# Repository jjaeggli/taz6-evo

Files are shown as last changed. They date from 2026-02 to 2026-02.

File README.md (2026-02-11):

# TAZ6-Evolution

- [Purpose](#purpose)
- [Summary](#summary)
- [Caution!](#caution)
- [Design Philosophy](#design-philosophy)
- [Current Progress](#current-progress)
- [BOM](#bom)
- [Printed Parts](#printed-parts)
- [Assembly Instructions](#assembly-instructions)
  - [Required Tools](#required-tools)
  - [Disassembly](#disassembly)
  - [Heat Set Inserts](#heat-set-inserts)
    - [Z1 Axis](#z1-axis)
    - [Bearing Block](#bearing-block)
    - [Mounting Plate](#mounting-plate)
  - [Assembly](#assembly)
    - [X-Axis Carriage](#x-axis-carriage)
    - [Z1-Axis Traveler](#z1-axis-traveler)
    - [X-Z Axis Tuning](#x-z-axis-tuning)
    - [Belt Binder](#belt-binder)
    - [Accessories](#accessories)

## Purpose

Allow the Lulzbot TAZ6 to experimentally support other tool options, and to improve the rigidity and performance of the toolhead.

## Summary

A series of evolutionary modifications for the Lulzbot TAZ6 and possibly other TAZ series 3D printers. The goal of the modifications are to allow adapting the printer to different toolhead designs by introducing modifications to the X-axis carriage, and to improve the rigidity of the toolhead by creating additional mount points. As a prerequisite, modifications must be made to the Z-axis to adjust the angle and position of the X-axis belt. The result is a series of evolutionary steps necessary to redesign the Taz while maintaining existing functionality at each step.

## Caution!

These designs have not yet been tested beyond one TAZ6 printer, and required troubleshooting and problem solving at each step. Individualized tweaks to the design may be required for your printer which were not required for mine. If you disassemble parts such as the original X-axis carriage to use the existing Igus bearings, this may destroy the part. These designs come without warranty, and any loss or damage is your responsibility.

* This design does not take into account the X or Z-max endstops, which are not used by Klipper
* Work on the left hand (motor side) Z-traveler is incomplete and untested

## Design Philosophy

* Move forward in reversable steps
* Reuse hardware from the original printer where possible
* Predict future use cases without setting specific untested requirements
* Design iteratively and start from scratch often
* (1) Make it work, (2) make it correct, (3) make it perform (pretty, optimal, light weight, etc...)

## Current Progress

- [x] Modification of the right Z-gantry traveler
  * reposition the idler pulley at the midpoint between the X rails.
  * convert the composite Igus bearing to LM10LUU (55mm) linear bearings to simplify design and assembly.
  * add affordances for future modifications (motor mount, dual X axis pulleys).
- [x] Modification of the X-carriage
  * reduce the overall width of the X carriage to 60 mm.
  * improve vertical and horizontal symetry of the carriage.
  * align the belt with the midpoint of the X-axis rails
  * improve the belt binder to reduce flexibility
  * add mount points for hard mounting components
- [x] Modification of the tool mount plate
  * add mount points to the plate to allow tools to be directly mounted to the plate.
  * add mount points for TAZ quick tool change mounts.
- [ ] Modify motor mount for right side (Z0)
  * adjustable belt tension on motor mount
  * support mulitple motor / belt positions
- [ ] Modify motor mount for left side (Z1)
  * support dual stepper motors
  * adjustable belt tension on motor mount

## BOM

* An assortment of M3 hex socket screws sizes 4mm - 25mm including nuts
* A handful of M3 poly washers
* A bunch of M3 5.5mm x 4mm heat set inserts
* (4) M5 heat set inserts (mine are M5 x 9.5) 
* (2) M5 x 25mm hex socket screw
* (2) M5 nylon lock nuts 
* (1) 20T GT2 idler pulley with 5mm bore
* (2) LM10LUU linear bearings
* (4) LM12UU IGUS solid polymer bearings RJ4JP
* (1) Lulzbot TAZ6 printer
* This list could be incomplete

## Printed Parts

| Qty | Material | Name | Desc |
|---|---|---|---|
| 2 | PETG | TAZ6-x-carriage-v0.5-BearingUniversal | Igus bearing block |
| 1 | PLA / ABS | TAZ6-x-carriage-v0.5-BeltTensioner | Belt tensioner / retainer |
| 1 | PLA / ABS | TAZ6-x-carriage-v0.5-EndStopClicker | Only necssary when not using the TazMount toolhead adapter |
| 1 | PLA / ABS | TAZ6-x-carriage-v0.5-MountingPlate | X-axis carriage mounting plate |
| 1 | PLA / ABS | TAZ6-x-carriage-v0.5-TazMount | Lower mounting bracket for TAZ quick mout toolheads |
| 1 | PLA / ABS | TAZ6-x-carriage-v0.5-TazMountTop | Upper mount point for TAZ quick mount toolheads |
| 1 | PETG | TAZ6-z-axis-v0.3-Z1-Axis | Right (Z1) axis |
| 0 | PETG | TAZ6-z-axis-v0.4-Z0-Axis | Left (Z0) axis - *unused* |

## Assembly Instructions

*These aren't really instructions per se, more like guidelines.*

### Required Tools

* 2.5 mm hex key
* 3 mm hex key
* 4 mm hex key
* Adjustable wrench or metric socket set
* Low temp soldering iron for insets
* Cubes of equal height (at least 40mm) that you can use as standoffs (such as stacked calibration cubes)

### Disassembly

Adjust the gantry height so that the standoff cubes are just barely held in place between the lower X-axis rod and the green lower Z-axis assembly on the right hand side. This will be used later in the process to ensure that the rods are attached squarely.

Disassemble and remove the X-axis belt, the X-axis rods, the X-axis carriage (removed from the rods), and the right top plate.

Unscrew the two M5 screws from the right lead screw nut (threaded flange). Reserve these screws. Remove the right Z-axis traveler. Reserve the green lead screw spacer.

Unplug the right stepper motor connector.

### Heat Set Inserts

Note: There are many available positions for heat set inserts - more than you will actually need. Install only the ones necessary for your specific use case at this point.

#### Z1 Axis

* (2) M3 inserts for securing the rods. (top and bottom)
* (2) M5 insers for attaching the lead screw nut. (12:00 and 6:00 position when facing the printer)

#### Bearing Block

* (2) M3 inserts on the top of one universal bearing block (this block will now be the top block)

#### Mounting Plate

All inserts on the mounting plate are optional. Hex nuts are used for all pull-through hardware and for convenience during prototyping. Mounting the *TAZ-EVO* toolhead components requires use of insets. 

### Assembly

#### X-Axis Carriage

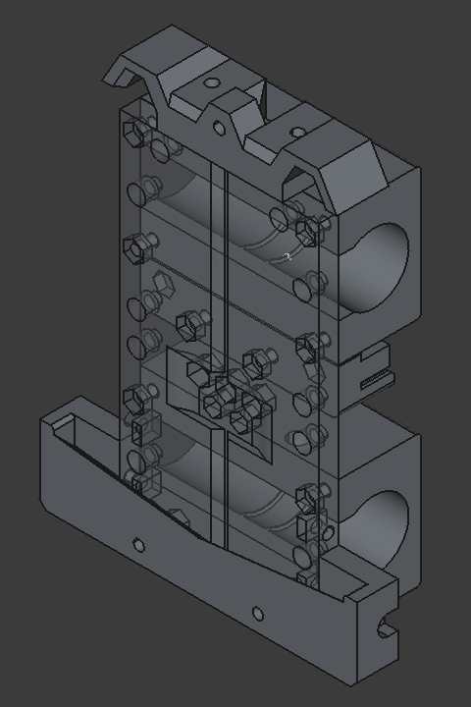
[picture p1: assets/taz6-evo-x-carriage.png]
X-carriage


* Sand and trim the inside of both `BearingUniversal` blocks.
* Snap Igus bearings in place. (Be careful as they do easily pinch skin)
* Test the blocks on one loose end of a rod. If the block is too tight / does not travel easily, remove the bearings and perform some additional sanding and trimming on the retaining rings inside the block.
* Fit (2) M3 nuts for the TAZ mount into the *back* of `MountingPlate` (the back is the side without the groove).
* Attach the bearing blocks with (4) M3 x 25mm screws and (4) M3 nuts for each block. The screws should be somewhat loose but still engaged in the nuts.

#### Z1-Axis Traveler

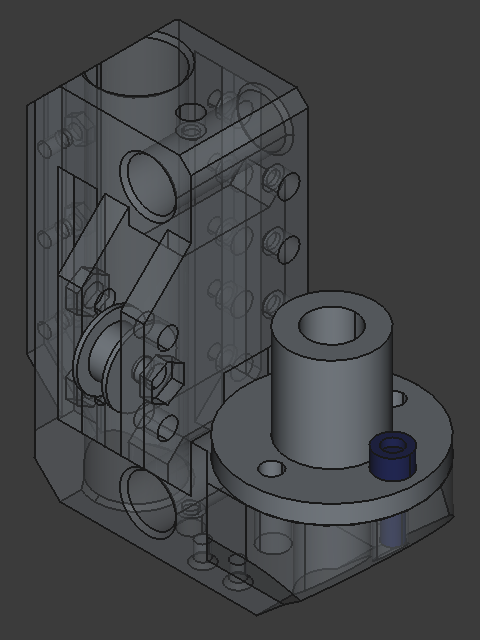
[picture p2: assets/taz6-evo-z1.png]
Z1-Axis


* Fit (1) LM10LUU bearing into position and secure with (3) M3 x 10mm screws and (3) M3 x 10mm nuts
* Fit (1) M5 x 25mm screw in place with the idler pulley in the center position and secure with the lock nut.
* Screw (2) M3 x (smallest that works) screw in each heat set insert. Test that when tightened the screw engages the rod and prevents movement. Leave loose.
* Slide the Z-axis traveler over the two rods, and slide it down to the bottom.
* Insert the X-axis rods through the traveler from the right hand side, so that they extend on each side.
* Slide the X-carriage over the the X-axis rods.
* Slide the X-axis rods throug the right Z-traveler until they reach the left Z-traveler, and use the standoff blocks to ensure that the rods are at the correct height.
* Add the green lead screw spacer, and then thread the lead screw nut until it is approximately in position. Thread the reserved M5 screws into the nut and adjust them until they are just loose.
* Using the spacer between the X-axis rods, and any other measurement tools at your disposal, ensure that the X-axis is square and level. Tighten grub screws on the left side and the M3 screws on the right side to secure the rods in place. 
* Ensure that the X-carriage still travels freely, and the lead screw turns easily.
* Reinstall the top plate on the Z-axis, ensuring that the extrusions are square when tightening.
* Follow the instructions below for tuning the X-Z axis

#### X-Z Axis Tuning

The X and Z axes intersect at the junction of the X-axis rails, and the Z-axis rail and lead screw. The Z-traveler holds the Z-axis linear bearing, the lead screw nut, the X-axis linear rails, and secures the belt. All of these parts must be properly aligned for the Z-traveler to move freely in the Z direction.

* At each step durring the assembly, the lead screw should be checked to ensure it rotates freely by turning it back and forth slightly. It should turn easily. If it is difficult to turn, the previous step introduced binding.
* Disconnnecting the power connector from the motor will ensure that there is not additional electromagnetic load on the motor (even when the printer is off)
* The X-axis rails oppose the force applied by the belt. If there is tension on the belt when the rails are loose, this can cause leadscrew binding. *You must loosen the belt before loosening the X-axis rails.*
* The X-axis belt must be loose when tuning the X-Z Axis.
* The squishy yellow-green spacer allows the leadscrew nut *tilt* to be properly aligned.
* When tightening the M4 screws on the lead screw nut, tighten them a quarter turn at a time, alternating between each, and checking the lead screw binding at each step. If the lead screw binds, loosen the screw and tighten the *opposite* screw.

#### Belt Binder

* The binding block holds the belt securely in place, and provides coarse tuning for belt tension.
* The stepper motor mount provides fine tuning for belt tension.
* Loosen the X-Axis stepper motor screws
* Thread the belt through the idler pulley on the right Z-axis
* Secure each end of the belt into the binding block so that the belt is as tight as possible.
* Use (2) M3 x 16mm screws, (2) M3 poly washers and (2) M3 nuts to secure the belt to the block, so that the head of the screw faces backward and the nut faces forward, and the tail of the belt goes to the top.
* Adjust the tension by pulling the stepper motor to the left. If There is not enough tension on the belt, loosen the motor mount and adjust the belt position on the block by 1 tooth. If necessary, move three of the stepper screws so that the motor rotates and provides additional slack to adjust the belt.

#### Accessories

* Ensure that either `TazMount` or `EndStopClicker` is installed before homing the printer *or you will hear bad noises*.
* Use (2) M3 x 12mm screws to attach either part to the toolhead.
* Move the X-carriage all the way to the left to test contact with the X-min microswitch.

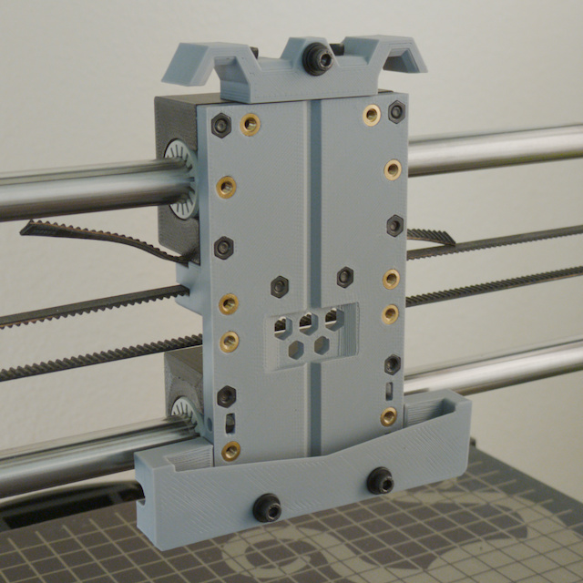
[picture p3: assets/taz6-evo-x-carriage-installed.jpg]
Installed


Printing

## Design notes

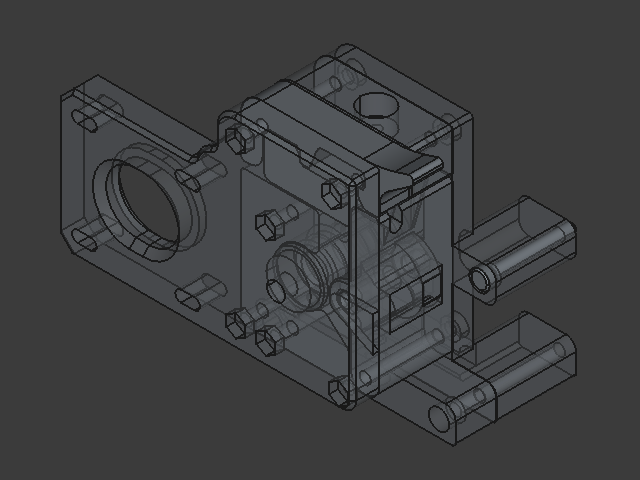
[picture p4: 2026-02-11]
assets/belted-extruder-direct.png

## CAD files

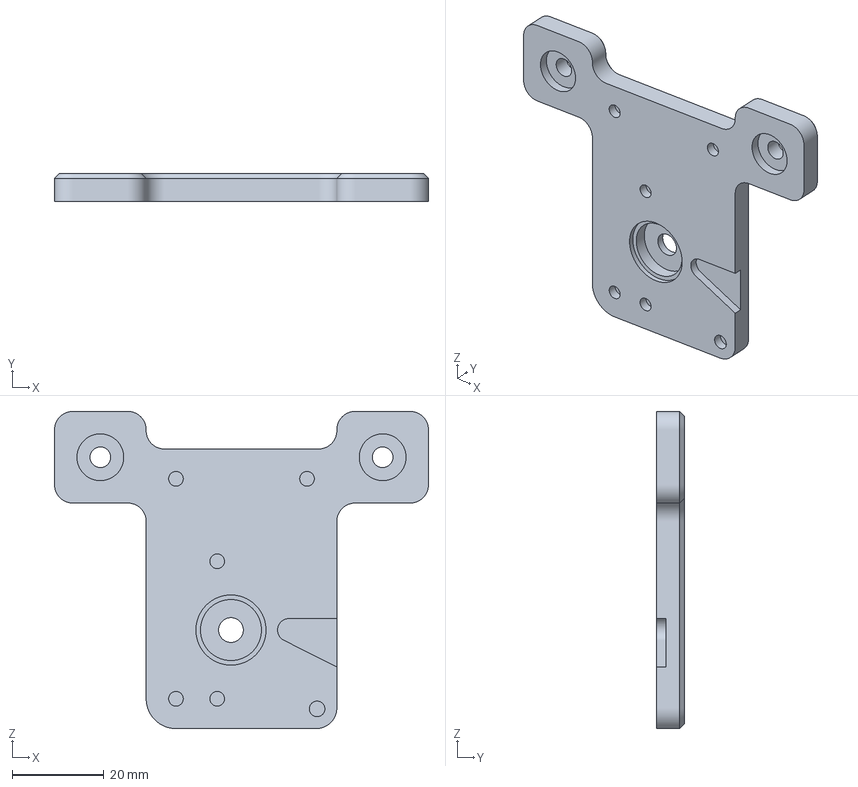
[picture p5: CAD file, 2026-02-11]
belted-extruder/3mf/dual_drive_extruder_v0.3-BackPlateBowden.3mf
81.6 x 6.00 x 69.2 mm

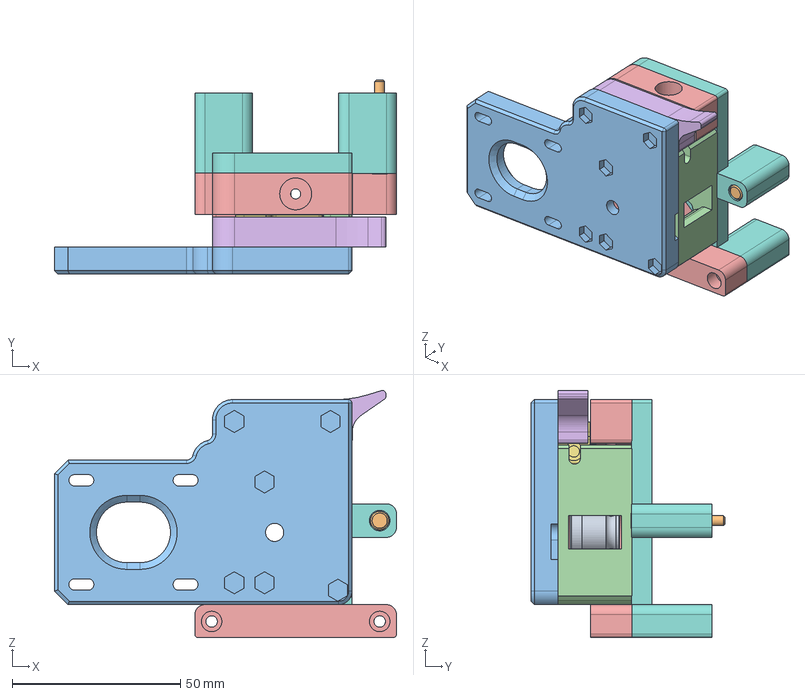
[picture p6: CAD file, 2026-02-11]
belted-extruder/cad/belted_extruder_v0.4.FCStd
101.8 x 57.8 x 73.5 mm
Drive Gear Body
Tensioner Body
Body-Lower
Latch-Body008
MountPlate

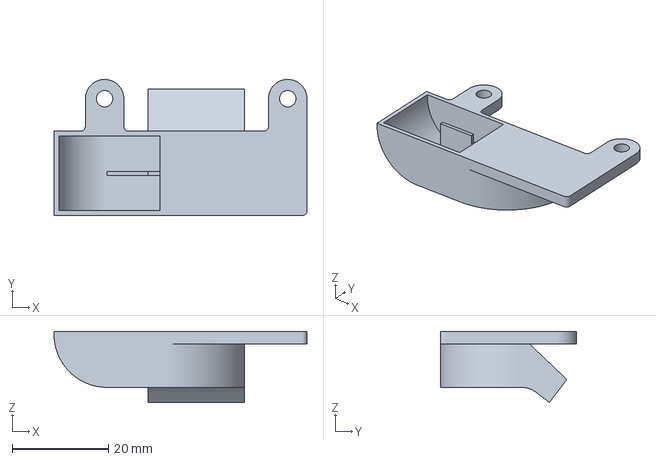
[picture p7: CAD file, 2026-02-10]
taz/3mf/TAZ-EVO-Dragon-v0.4-SimplePartCoolingDuct.3mf
52.5 x 28.2 x 14.7 mm

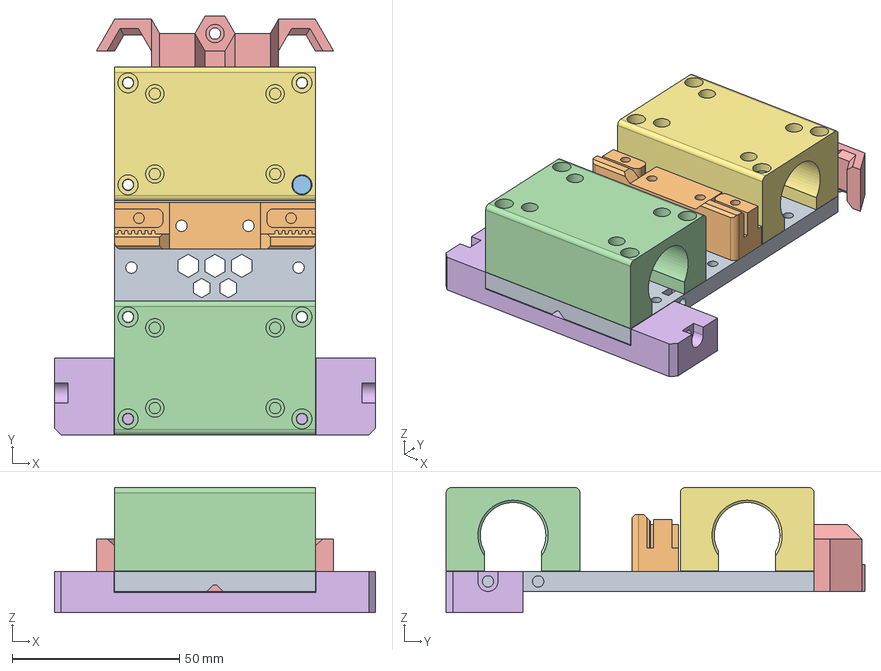
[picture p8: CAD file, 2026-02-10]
taz/cad/TAZ6-x-carriage-v0.5.FCStd
96.0 x 125.2 x 37.4 mm
MountingPlate
BeltTensioner
BearingUniversalClone001
TazMountTop
TazMount
BearingUniversalBody

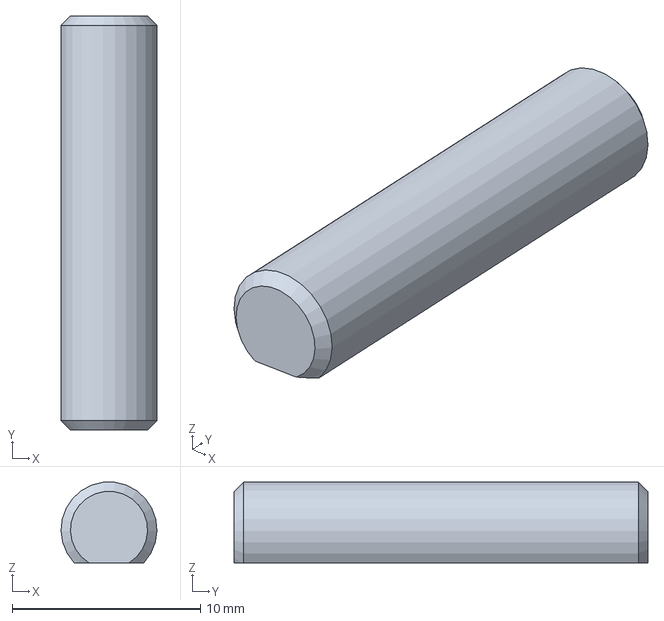
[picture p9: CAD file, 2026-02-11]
belted-extruder/3mf/dual_drive_extruder_v0.3-AxlePin.3mf
5.10 x 22.0 x 4.28 mm

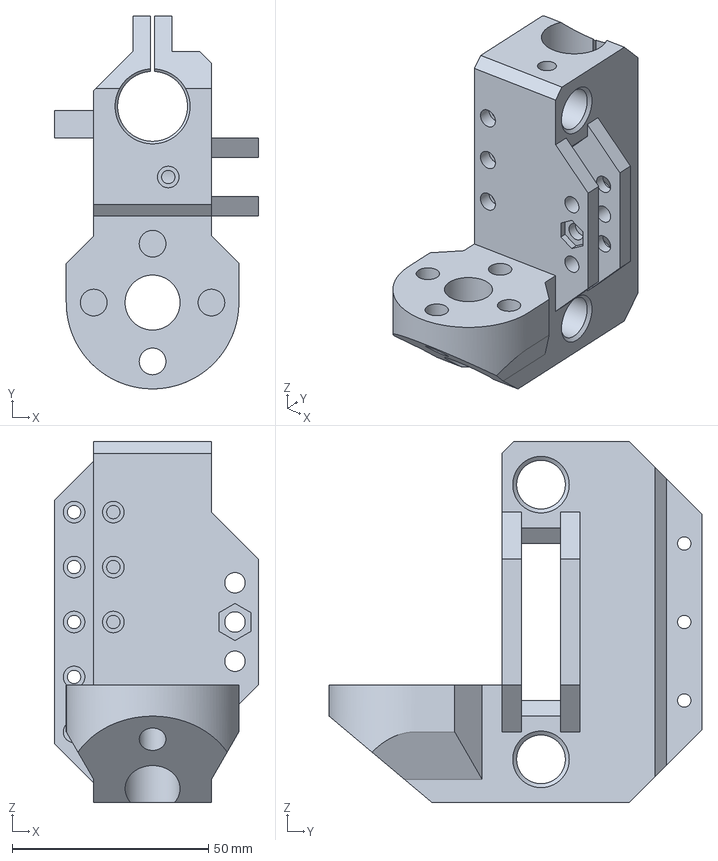
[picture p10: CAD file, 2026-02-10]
taz/3mf/TAZ6-z-axis-v0.3-Z1-Axis.3mf
52.0 x 95.0 x 92.0 mm

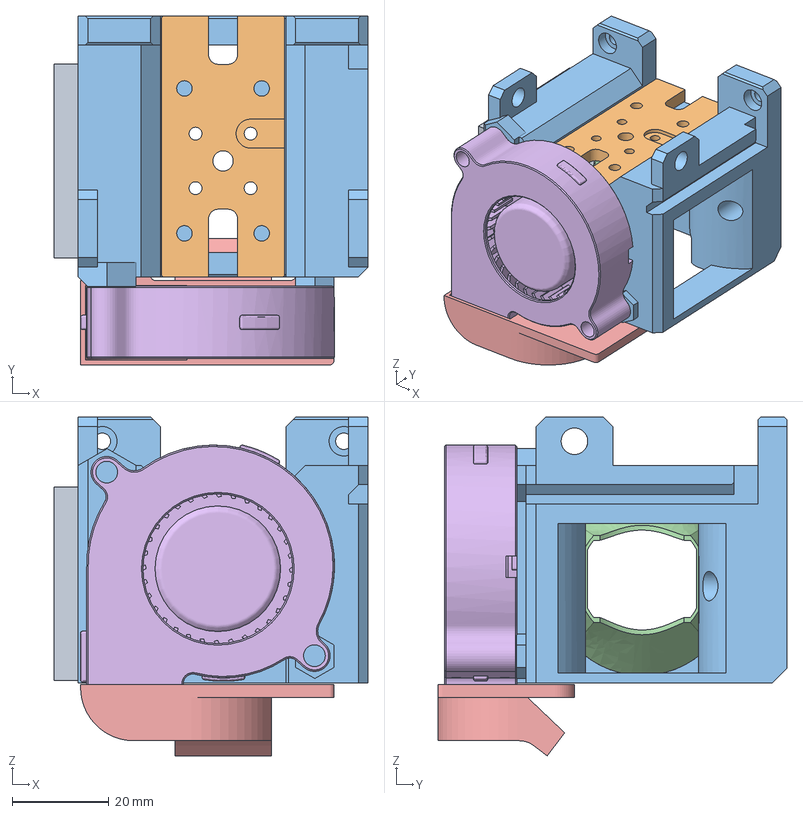
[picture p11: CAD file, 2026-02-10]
taz/cad/TAZ-EVO-Dragon-v0.4.FCStd
65.0 x 72.3 x 70.1 mm
BooleanBody
HeatBreakDuctBody
Radial_Fan_50x15_v8

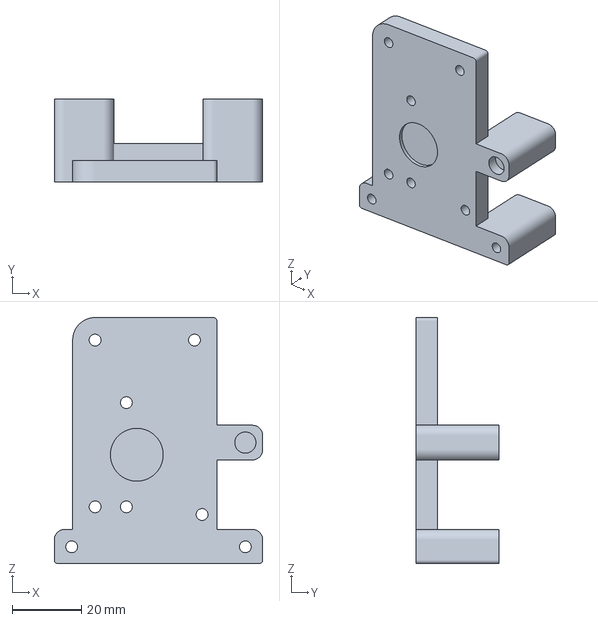
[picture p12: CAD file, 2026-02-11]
belted-extruder/3mf/dual_drive_extruder_v0.4-BackPlateDirectTaz.3mf
60.0 x 24.0 x 70.8 mm

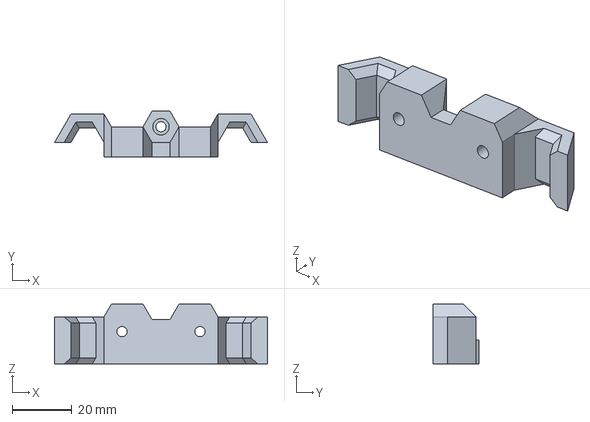
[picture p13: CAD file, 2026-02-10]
taz/3mf/TAZ6-x-carriage-v0.5-TazMountTop.3mf
71.0 x 15.2 x 20.0 mm

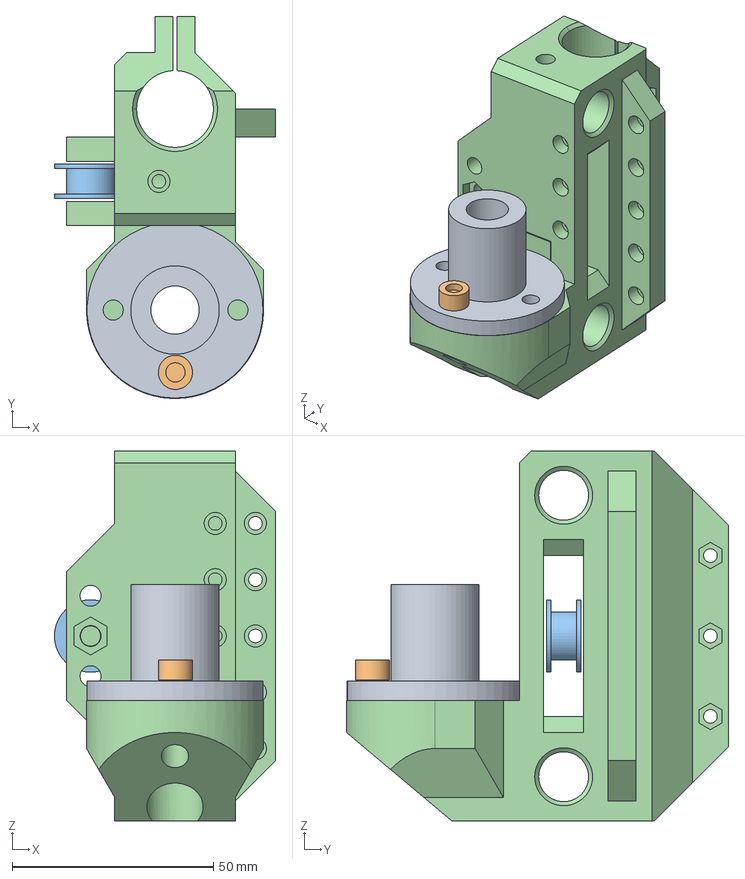
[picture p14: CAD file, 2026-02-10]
taz/cad/TAZ6-z-axis-v0.4.FCStd
55.0 x 95.0 x 92.0 mm
PulleyCenter
UnionBodyMirrored

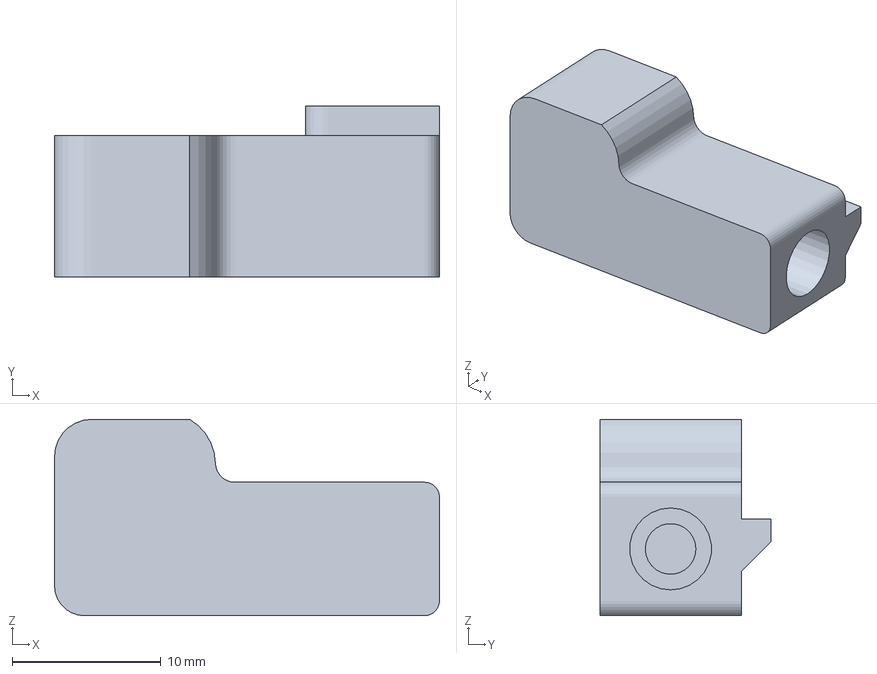
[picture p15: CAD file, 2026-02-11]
belted-extruder/3mf/dual_drive_extruder_v0.3-LatchShuttle.3mf
25.8 x 11.5 x 13.2 mm

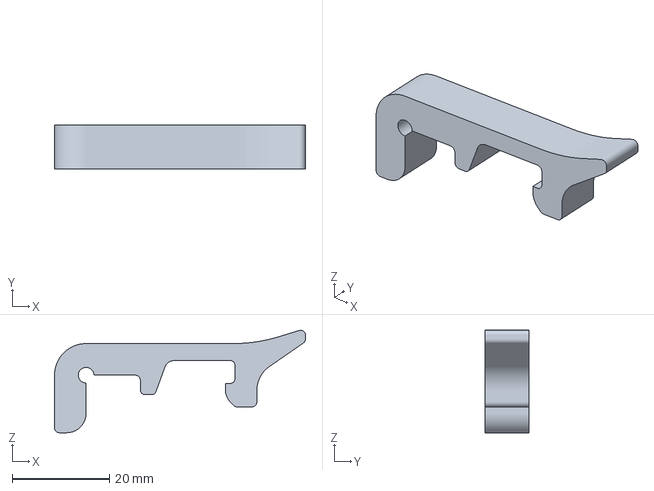
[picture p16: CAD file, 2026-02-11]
belted-extruder/3mf/dual_drive_extruder_v0.3-TensionerLatch.3mf
51.6 x 9.00 x 21.1 mm

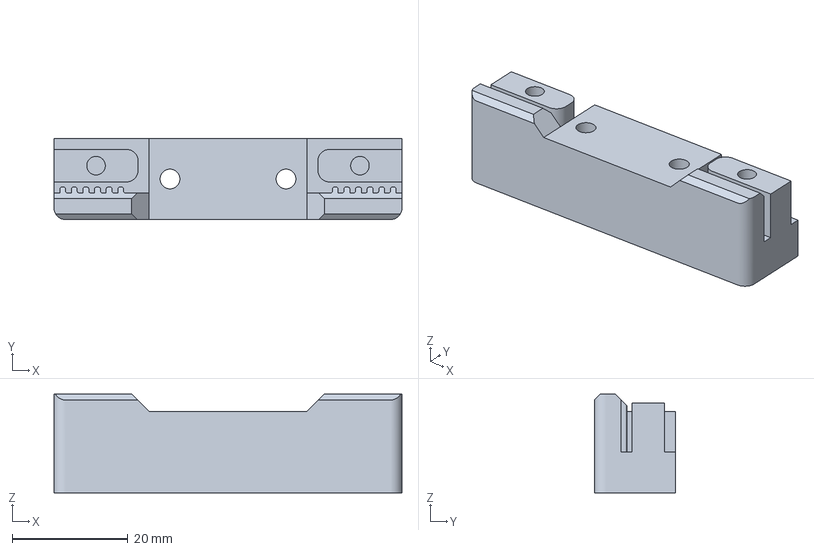
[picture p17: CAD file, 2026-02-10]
taz/3mf/TAZ6-x-carriage-v0.5-BeltTensioner.3mf
60.0 x 14.0 x 17.0 mm

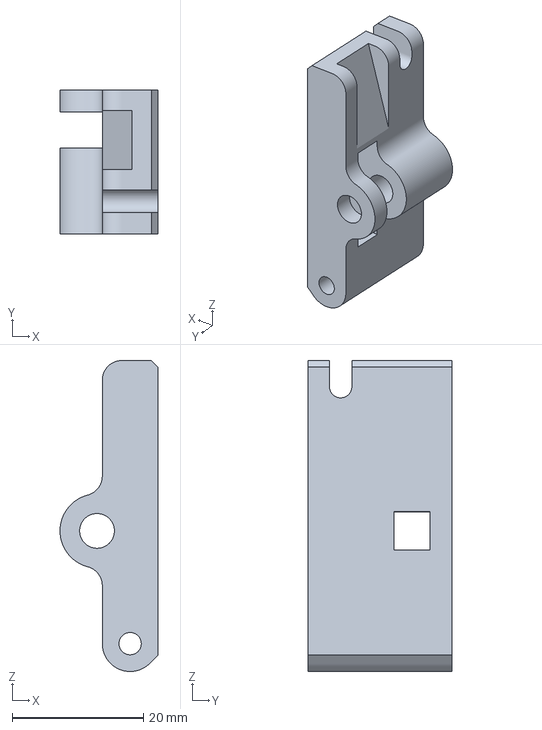
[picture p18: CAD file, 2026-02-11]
belted-extruder/3mf/dual_drive_extruder_v0.3-BearingTensioner.3mf
14.9 x 22.0 x 47.5 mm

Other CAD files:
taz/3mf/TAZ6-z-axis-v0.4-Z0-Axis.3mf
taz/3mf/TAZ6-x-carriage-v0.5-EndStopClicker.3mf
belted-extruder/3mf/dual_drive_extruder_v0.3-Tensioner.3mf
taz/3mf/TAZ-EVO-Dragon-v0.4-HotendMountPlate.3mf
belted-extruder/3mf/78t_pulley_v0.1-78t_pulley.3mf
belted-extruder/3mf/dual_drive_extruder_v0.3-BodyLowerBowden.3mf
belted-extruder/3mf/dual_drive_extruder_v0.3-MotorMount.3mf
belted-extruder/3mf/dual_drive_extruder_v0.4-BodyLower.3mf
taz/3mf/TAZ-EVO-Dragon-v0.4-CombinedTool.3mf
taz/3mf/TAZ-EVO-Dragon-v0.4-HeatBreakFanDuct.3mf
taz/3mf/TAZ-EVO-Dragon-v0.4-HotendMountPlate-Conductor.3mf
taz/3mf/TAZ6-x-carriage-v0.5-BearingUniversal.3mf
taz/3mf/TAZ6-x-carriage-v0.5-MountingPlate.3mf
taz/3mf/TAZ6-x-carriage-v0.5-TazMount.3mf

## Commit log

2026-02-10 Add project files for TAZ6-EVO
    [TAZ-EVO-Dragon-v0.4-CombinedTool.3mf, TAZ-EVO-Dragon-v0.4-HeatBreakFanDuct.3mf, TAZ-EVO-Dragon-v0.4-HotendMountPlate-Conductor.3mf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]
2026-02-11 add belted extruder; rename parts/ to taz/; add images
    [78t_pulley_v0.1-78t_pulley.3mf, TAZ-EVO-Dragon-v0.4-CombinedTool.3mf, TAZ-EVO-Dragon-v0.4-HeatBreakFanDuct.3mf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]
